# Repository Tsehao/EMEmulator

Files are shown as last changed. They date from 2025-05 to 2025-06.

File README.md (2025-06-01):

# EMEmulator
This project provides a complete set of 3D-printable models and driver scripts, enabling researchers to quickly build an eye movement emulator through for eye-tracking sensor or eye tracker testing.

All components of the system are fully customizable to suit different research needs. You can modify the head model design, choose different types of servo motors, or adjust the  configuration of eye movement system depending on your goals.

The head model used in this project is derived from https://www.thingiverse.com/

The eye movement mechanism design is inspired by the work of https://www.youtube.com/watch?v=ihXxbQefl1c&t=778s

# Demo Video
1. eye movement :

https://github.com/user-attachments/assets/1db18268-8950-4e94-82a0-a7d7bd538a73

2. Tracking by Tobii G2:

https://github.com/user-attachments/assets/09b8be72-da56-41d0-82cc-6a8103d74bc8

# Project Contents
This repository includes the following components:
1. 3D printing Files
   Pre-sliced models (Bambu Studio compatible) for:
      Head model
      Eyeball base
      Screen base
      Servo motor mounts and linkages
   —— the installation completion diagram of eye movement structure: iShot_2025-05-25_11 10 48

3. Parts List
   Complete BOM (Bill of Materials) with all required components for assembling the eye movement emulator.
5. Control software
   Python script featuring:
      Real-time marker tracking uding OpenCV
      Coordinate calcualtion for gaze position
      Servo motor control interface for precise eye movement simulation

# Assembly Instructions
Coming Soon. A full tutorial video will be publishsed on our social media platforms. If you have any questions, please contact Huang, Zehao (Tsehao.huang@outlook.com)

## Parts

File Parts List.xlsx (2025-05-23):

PN | Catefory | Name | Number | Material | Source | Price（CNY） | Notes
1 | Head | Forehead | 1 | PLA | 3D print
2 |  | Head | 1 | PLA | 3D print
3 |  | Ear support | 2 | PLA | 3D print
4 |  | Pedestal | 1 | PLA | 3D print
5 |  | Camera | 1 | Electronic | Purchase from: https://item.taobao.com/item.htm?detail_redpacket_pop=true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 | 221
6 | Eyeball | Eye ball base | 8 | PLA | 3D print
7 |  | Corneal type glass | 8 | Glass | Purchase from: https://item.taobao.com/item.htm?_u=n1k2tkpd44e&id=615647794057&spm=a1z09.2.0.0.4d882e8dzwaAAc | 0.13
8 | Eye Movement | Servo board | 2 | PLA | 3D print
9 |  | Bus servo | 4 | Metal | Purchase from: https://item.taobao.com/item.htm?abbucket=9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 | 1312
10 |  | Servo control | 1 | Electronic | Purchase from: https://item.taobao.com/item.htm?id=600130669485 | 25.8
11 |  | External power supply | 1 | Electronic | Purchase from: https://item.taobao.com/item.htm?id=616609736473 | 18
12 |  | Eye ball bracket （half） | 4 | PLA | 3D print
13 |  | Horizontal steering knuckle | 2 | PLA | 3D print
14 |  | Vertical steering knuckle | 2 | PLA | 3D print
15 |  | Support arm | 2 | PLA | 3D print
16 |  | Steering rod head - form 1 | 4 | PLA | 3D print
17 |  | Steering rod head - form 2 | 4 | PLA + Metal | Purchase from: https://item.taobao.com/item.htm?id=525034665247&sku_properties=31309%3A1654744869 | 0.21
18 |  | Steering rod | 4 | Metal | Purchase from: https://item.taobao.com/item.htm?id=525052601020&sku_properties=31309%3A101083 | 5.6 | M2 * 45mm
19 |  | Small size bearings | 18 | Metal | Purchase from: https://detail.tmall.com/item.htm?id=611796709407 | 23.4 | insdie diameter * outside diameter * thickness = 2*4*2
20 |  | Large size bearings | 4 | Metal | Purchase from: https://detail.tmall.com/item.htm?id=611796709407 | 4 | insdie diameter * outside diameter * thickness = 3*6*3
21 |  | Small size screw | 4 | Metal | Purchase from: https://detail.tmall.com/item.htm?id=641493636015 | 0.208 | M2 * 8mm
22 |  | Large size screw | 4 | Metal | Purchase from: https://detail.tmall.com/item.htm?id=641493636015 | 0.256 | M2 * 12mm
23 | Additional materials | Rail | 1 | Metal | Purchase from: https://item.taobao.com/item.htm?id=683336507040 | 499.82
24 |  | Display base | 2 | PLA | 3D print
25 |  | UV glue | 1 | Glue | Purchase from: https://detail.tmall.com/item.htm?detail_redpacket_pop=true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 | 9.2

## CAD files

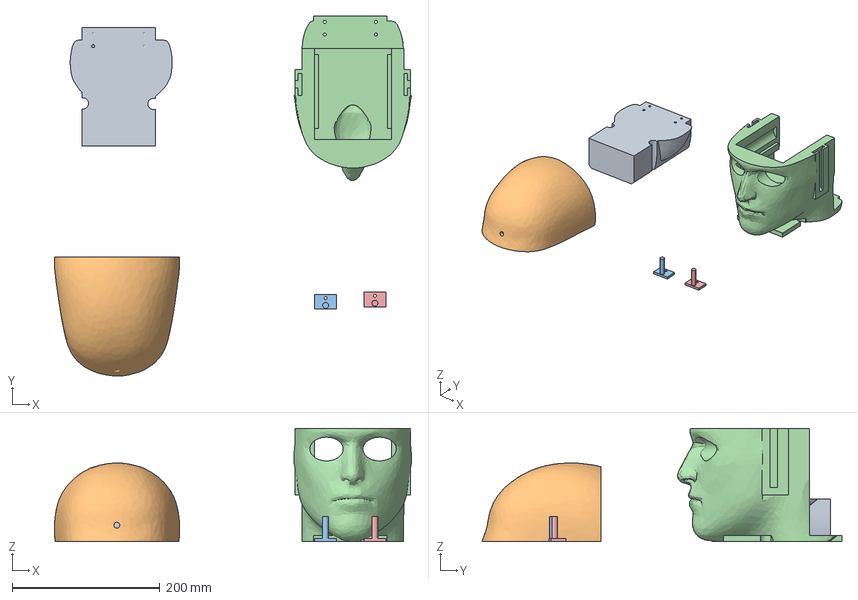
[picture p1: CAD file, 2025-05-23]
3D Printing Files/01_Head.3mf
482.8 x 486.6 x 153.2 mm
实体-头.step_B
实体-头.step_A_A
耳托支撑.step x 2
实体-头-中-可活动耳托.step

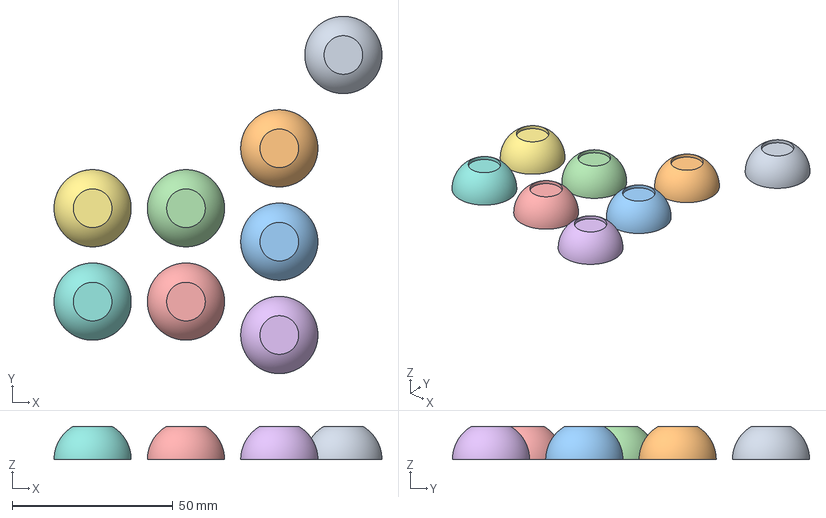
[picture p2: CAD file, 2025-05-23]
3D Printing Files/02_iris vision eye ball with different pupil size.3mf
101.9 x 111.0 x 10.4 mm
2mm x 2
3mm x 2
4mm x 2
5mm x 2

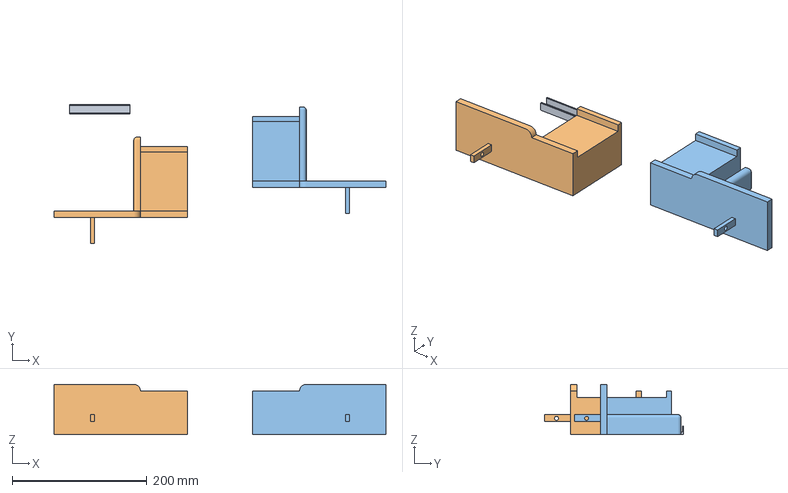
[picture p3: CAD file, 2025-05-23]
3D Printing Files/03_Screen_holder.3mf
493.6 x 207.0 x 75.0 mm
02_显示器基座-顶部卡扣.step
02_显示器基座-右侧.step
02_显示器基座-左侧.step

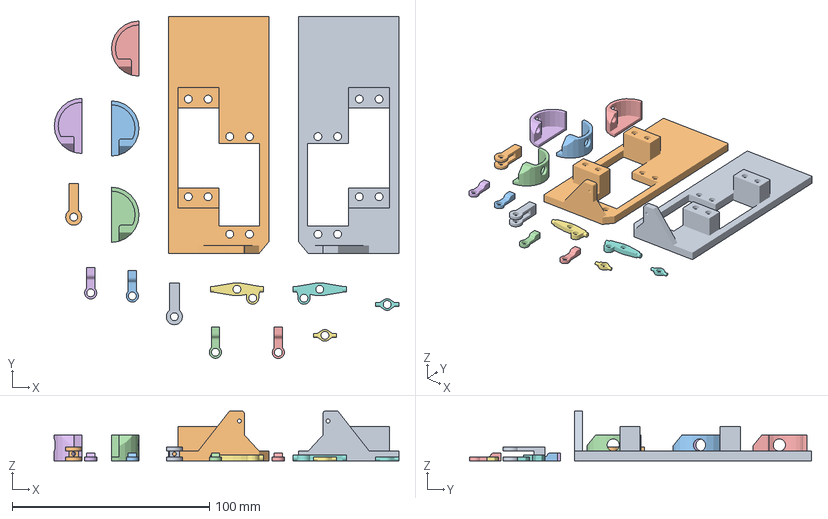
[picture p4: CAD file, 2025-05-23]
3D Printing Files/04_Servo_holder.3mf
174.7 x 173.4 x 25.2 mm
04_Board_Right_×1_fixed.stl
05_Board_Left_×1_fixed.stl
02_Eye_holder_Right_x2_V1.step x 2
03_Eye_holder_Left_x2_V1.step x 2
07_Holder_Vertical_Connector_Right_×1.stl
08_Holder_Vertical_Connector_Left_×1.stl
07_Board_Holder_Connector_×2.stl x 2
06_Servo_Holder_Connector_×4.stl x 4
09_Holder_Horizontal_Connector_×2.stl x 2

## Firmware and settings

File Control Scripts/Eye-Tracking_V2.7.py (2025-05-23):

# -*- coding: utf-8 -*-
"""
Created on Fri Sep 27 10:23:33 2024

@author: HZH

Servo Tracking using Usb Camera and Bus Servo
"""

import math
import serial
import cv2

import os
#current_path = os.path.dirname(os.path.abspath(__file__))
#os.chdir(current_path)
os.chdir(r'/Users/huangzehao/Desktop/Project/[科研] Pupil_Size_Test/Data_Exp_FIles/Exp_Scripts_add_Screen_marker_202503/Eye_SImulator')
from uservo import UartServoManager

class BusServo:
    def __init__(self, com_port, center_angle=None, speed=50):
        self.port = com_port
        self.center_angle = center_angle if center_angle else [16, -16, 8, 8]
        self.speed = speed
        self.uservo = None
        self.center_marker = [0,0,0,0]
        self.current_angle = [0,0,0,0]
        self.angle_limits =  {
                            0: (-22, 44),
                            1: (-50, 4),
                            2: (-15, 34),
                            3: (-21, 55)
                            }
        
        self.backlash = {0:-0.6, 1:0.6, 2:0.6, 3:-1}
        self.last_direction = [1, 1, 1, 1] # 1:left; -1:right
        
    def init_server(self):
        uart = serial.Serial(
            port=self.port,
            baudrate=115200,
            parity=serial.PARITY_NONE,
            stopbits=1,
            bytesize=8,
            timeout=0
        )
        self.uservo = UartServoManager(uart, is_debug=True)
        print(f'Bus Server started at {self.port}')

    def recenter(self):
        for i in range(4):
            self.uservo.set_servo_angle(i, self.center_angle[i], self.speed)
        self.current_angle = self.center_angle[:]
        print('Eye direction reset complete')
        
    def recenter_marker(self, angle):
        for i in range(4):
            tar_angle = self.center_angle[i] + angle[i]
            self.uservo.set_servo_angle(i, tar_angle, self.speed)
            self.center_marker[i] = tar_angle

    def send_servo_angles(self, angle):
        
        for i in range(4):
            
            if angle[i] == 0:
                pass
            else:
                tar_angle = self.center_angle[i] + angle[i]
                
                # backlash compensation for reverse motion
                current = self.current_angle[i]
                
                # direction detection
                if tar_angle - current >= 0:
                    direction = 1
                else:
                    direction = -1
                
                if abs(tar_angle - current) >= 2:
               
                    if direction != self.last_direction[i]:
                        if direction == 1:
                            tar_angle += self.backlash[i]
                        elif direction == -1:
                            tar_angle -= self.backlash[i]
                
                # update last direction
                self.last_direction[i] = direction
                
                # angle limition for protect the eyeholder
                lower, upper = self.angle_limits[i]
                tar_angle = max(lower, min(upper, tar_angle))
                        
                # # servo moving
                # step = 1 if tar_angle > current else -1
                # end_angle = int(tar_angle + step)
                
                # for step_angle in range(current, end_angle, step):
                #     self.uservo.set_servo_angle(i, step_angle, self.speed)
                #     self.current_angle[i] = step_angle
                
                self.uservo.set_servo_angle(i, tar_angle, self.speed)
                self.current_angle[i] = tar_angle
            

class CameraHandler:
    def __init__(self, camera_index=1, marker_size=3.5, ipd=6.5, tar_dis=66, zcamera=5.5):

        self.marker_size = marker_size
        self.ipd = ipd
        self.tar_dis = tar_dis
        self.zcamera = zcamera
        
        self.camera = cv2.VideoCapture(camera_index)
        self.camera.set(cv2.CAP_PROP_FRAME_WIDTH, 1920)
        self.camera.set(cv2.CAP_PROP_FRAME_HEIGHT, 1080)
        
        # load the predefined ArUco dictionary
        self.aruco_dict = cv2.aruco.getPredefinedDictionary(cv2.aruco.DICT_5X5_250)
        self.parameters = cv2.aruco.DetectorParameters()

        if not self.camera.isOpened():
            raise ValueError("Camera initialization failed")
        print("Camera initialized successfully")

    def capture_frame(self):
        ret, frame = self.camera.read()
        if not ret:
            raise ValueError("Failed to capture frame")
        return frame

    def detect_marker(self, frame):
        corners, ids, _ = cv2.aruco.detectMarkers(
            frame,
            self.aruco_dict,
            parameters = self.parameters
        )

        if ids is not None:
            ids = ids.flatten()
            
            if ids[0] ==24:
                for marker_corner, marker_id in zip(corners, ids):
                    corners = marker_corner.reshape((4,2))
                    (top_left, top_right, bottom_right, bottom_left) = corners
        
                    # compute marker center
                    center_x = int((top_left[0] + bottom_right[0]) / 2.0)
                    center_y = int((top_left[1] + bottom_right[1]) / 2.0)
        
                    # compute frame center
                    image_center_x = frame.shape[1] // 2
                    image_center_y = frame.shape[0] // 2
        
                    # calculate distances
                    distance_x = center_x - image_center_x
                    distance_y = center_y - image_center_y
        
                    marker_len_pix = math.sqrt((top_left[0] - top_right[0]) ** 2 +
                                               (top_left[1] - top_right[1]) ** 2)
        
                    pix2cm = self.marker_size / marker_len_pix
        
                    return distance_x * pix2cm, distance_y * pix2cm
                return None

    def calculate_angles(self, cood_x, cood_y):
        # Calculate X angles for the left servo
        if cood_x >= 0:
            alpha4 = math.degrees(math.atan((self.ipd / 2 + cood_x) / self.tar_dis))
            alpha3 = math.degrees(math.atan((self.ipd / 2) / self.tar_dis))
            alpha2 = abs(alpha4) - abs(alpha3)
        elif cood_x < 0 and cood_x > -self.ipd / 2:
            alpha4 = math.degrees(math.atan((self.ipd / 2 - abs(cood_x)) / self.tar_dis))
            alpha3 = math.degrees(math.atan((self.ipd / 2) / self.tar_dis))
            alpha2 = -(abs(alpha3) - abs(alpha4))
        elif cood_x <= -self.ipd / 2:
            alpha5 = math.degrees(math.atan((abs(cood_x) - self.ipd / 2) / self.tar_dis))
            alpha3 = math.degrees(math.atan((self.ipd / 2) / self.tar_dis))
            alpha2 = -(abs(alpha5) + abs(alpha3))
        deg_x_l = round(alpha2, 1)

        # Calculate X angles for the right servo
        alpha3_r = math.degrees(math.atan((self.ipd / 2) / self.tar_dis))
        if cood_x < 0:
            alpha4_r = math.degrees(math.atan((self.ipd / 2 + abs(cood_x)) / self.tar_dis))
            alpha2_r = - (alpha4_r - alpha3_r)
        elif cood_x >= 0 and cood_x < self.ipd / 2:
            alpha4_r = math.degrees(math.atan((self.ipd / 2 - cood_x) / self.tar_dis))
            alpha2_r = alpha3_r - alpha4_r
        elif cood_x >= self.ipd / 2:
            alpha4_r = math.degrees(math.atan((cood_x - self.ipd / 2) / self.tar_dis))
            alpha2_r = alpha4_r + alpha3_r
        deg_x_r = round(alpha2_r, 1)

        # Calculate Y angles
        beta3 = math.degrees(math.atan(self.zcamera / self.tar_dis))
        if cood_y > 0:
            beta4 = math.degrees(math.atan((self.zcamera + cood_y) / self.tar_dis))
            beta2 = beta4 - beta3
        elif cood_y <= 0 and cood_y > -self.zcamera:
            beta4 = math.degrees(math.atan((self.zcamera - abs(cood_y)) / self.tar_dis))
            beta2 = -(beta3 - beta4)
        elif cood_y <= -self.zcamera:
            beta4 = math.degrees(math.atan((abs(cood_y) - self.zcamera) / self.tar_dis))
            beta2 = - (beta3 + beta4)
        deg_y = round(beta2, 1)

        return deg_x_r*0.5, -deg_y, deg_y, deg_x_l*0.5
    
    def release_camera(self):
        self.camera.release()
        cv2.destroyAllWindows()

def main():
    cam_handler = CameraHandler(camera_index=0)
    servo = BusServo(com_port="/dev/cu.usbserial-110")
    servo.init_server()
    
    servo.recenter()

    try:
        while True:
            frame = cam_handler.capture_frame()
            marker_position = cam_handler.detect_marker(frame)
            
            if marker_position:
                cood_x, cood_y = marker_position
                angles = cam_handler.calculate_angles(cood_x, cood_y)
                print("Servo angles:", servo.current_angle)
                servo.send_servo_angles(angles)

            # display the frame for visualization
            cv2.imshow("Camera Feed", frame)
           
            if cv2.waitKey(1) & 0xFF == ord('q'):
                break


    except Exception as e:
        print("Error:", e)

    finally:
        servo.recenter()
        cam_handler.release_camera()
        
        
if __name__ == '__main__':
    main()
    
    
   

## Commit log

2025-05-23 Add files via upload
    3D printing files
    [01_Head.3mf, 02_iris vision eye ball with different pupil size.3mf, 03_Screen_holder.3mf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]
2025-05-23 Create 3D Printing Files
